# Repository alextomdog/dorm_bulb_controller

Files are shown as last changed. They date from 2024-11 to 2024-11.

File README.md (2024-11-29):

# 项目概述
这是一个用于在寝室中不用下床开关灯的， 将esp8266作为服务器，通过手机web端进行控制舵机运动从而拨动开关的一个项目。

# 演示链接和焊接视频
焊接视频：https://www.bilibili.com/video/BV1LpzrY1Ee3/?vd_source=3774f0978f9f143e4c2fcfed1f5bf447
演示视频：https://www.bilibili.com/video/BV1DSzBYhEJo/

# 功能
1.使用电池，可以实现断电后继续运行

2.支持充电功能

3.使用wifi传输数据

# 物料清单
## 材料
-----------------
| 物料名称 | 数量  |
| :---: | :---: |
| esp8266开发板 | 1 |
| 导线 | 若干  |
| sg90舵机 | 1 |
| SS12F48开关 | 1 |
| M2x10十字头螺栓 | 8 |
| M2螺母 | 4 |
| M3x5十字头螺栓 | 2 |
| tp4056锂电池充电模块 | 1 |
| 18650锂电池 | 1 |
| 18650正负极电池片(一对) | 2 |
| s9013三极管(npn) | 1 |
| 3d打印外壳配件-框架底座(./stl目录) | 1 |
| 3d打印外壳配件-电池盖子(./stl目录) | 1 |
> Note

可以访问：https://makerworld.com/zh/models/832762#profileId-777419 
使用A1Mini 通过bambuStudio打开从而进行打印

## 工具
-----------------
| 工具名称 | 数量  |
| :---: | :---: |
| 锡膏 | 1 |
| 烙铁丝 | 1 |
| 电烙铁 | 1 |
| 剥线钳(可选) | 1 |
| 十字头螺丝刀 | 1 |

# 代码下载使用
1.确保电脑安装了`arduino IDE`

2.确保在`arduino IDE`中配置了`esp8266`的环境

3.下载相关库文件
```c
ESPAsyncTCP
ESPAsyncWebServer
ArduinoJson
Servo
```

4.将代码文件`./program/program.ino`上传到esp8266中

# 电路连接图
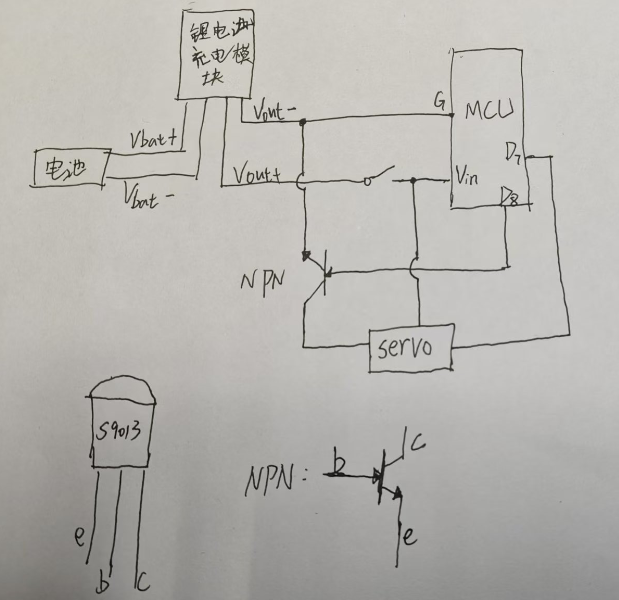
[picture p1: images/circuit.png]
circuit


# web端的使用说明

1. 手机连接到esp8266的wifi，默认wifi名称`dormitory`, 密码为`123456789`(可以在后期web页面的`settings`选项卡中进行修改)
   
2. 打开浏览器，输入静态ip地址:`192.168.192.1`，即可进入web页面进行控制
   
3. web端展示如下图，代码细节参考`/web_page/index.html`文件
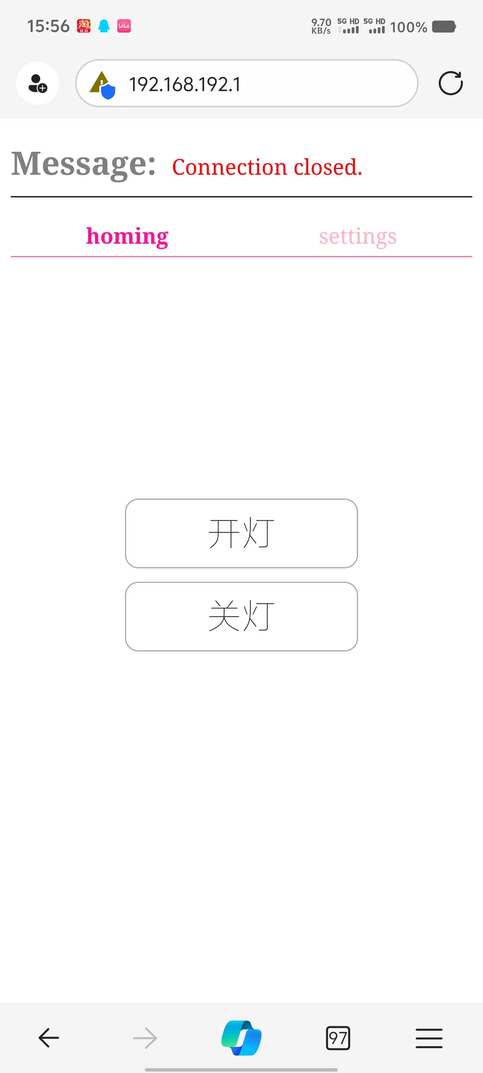
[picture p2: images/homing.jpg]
homing

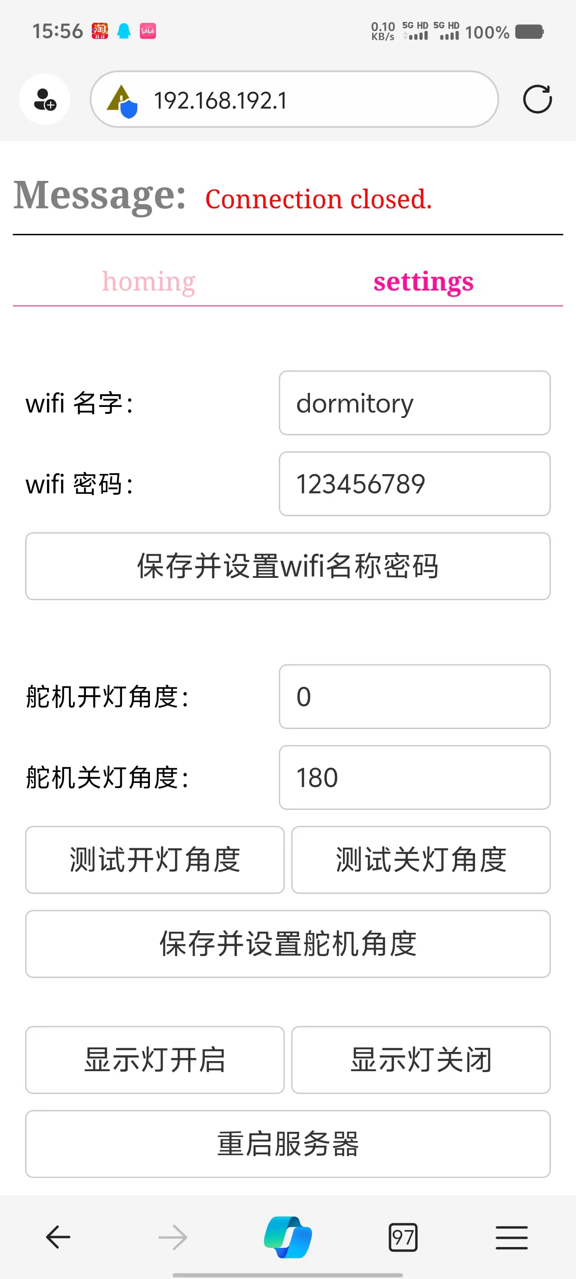
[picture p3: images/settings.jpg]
settings


# 其他说明

1.`/compress`文件夹放置的是用来压缩`html`文件的python代码，使用方法如下：
> `python compress.py path/to/your/html_file`

2.在进行开关灯之前

3.如果遇到连接到esp_wifi之后无法打开静态`ip`地址的情况，请断开数据流量之后再次从浏览器中打开`192.168.192.1`这个`ip`地址。存在部分手机如果检测到当前的wifi无法连接到互联网从而选择会走流量，导致无法访问`ip`地址。

4.连接到esp_wifi之后，是**无法访问互联网**的，需要断开连接之后才可以继续上网

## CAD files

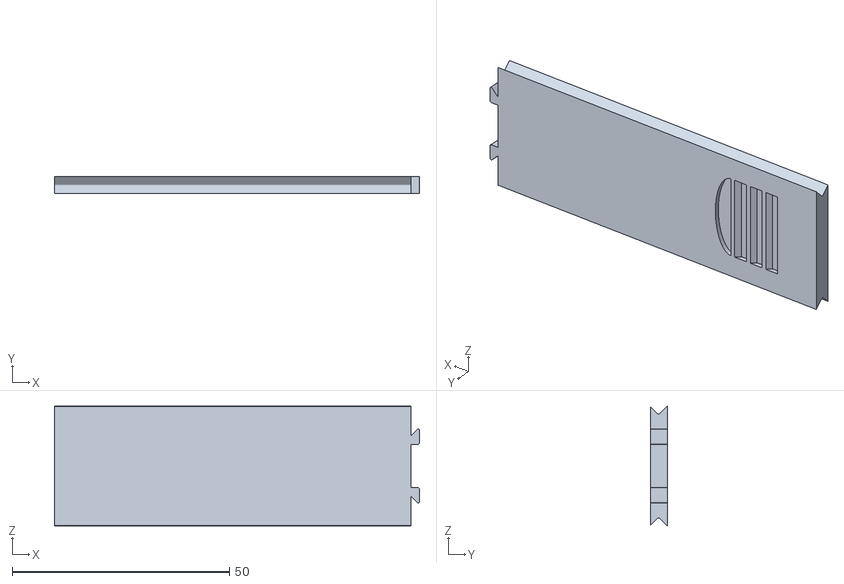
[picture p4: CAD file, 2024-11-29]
stl/电池盖子.STL
84.0 x 3.85 x 27.6

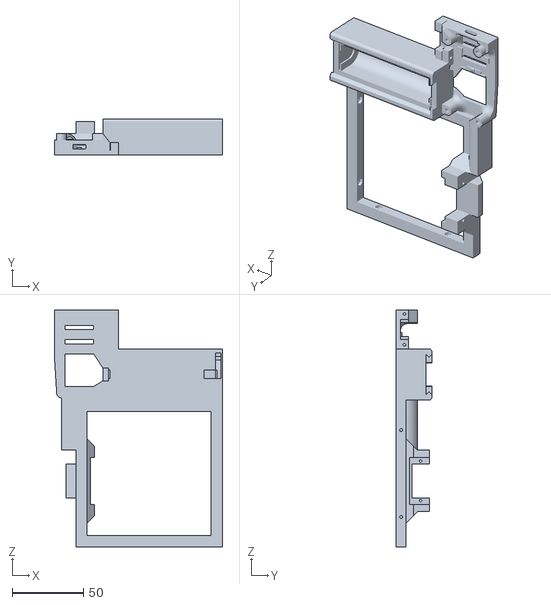
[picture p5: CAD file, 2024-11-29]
stl/框架底座.STL
118.0 x 25.0 x 166.2

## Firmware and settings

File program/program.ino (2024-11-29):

#include <ESP8266WiFi.h>
#include <ESPAsyncTCP.h>
#include <ESPAsyncWebServer.h>
#include <ArduinoJson.h>
#include <FS.h> // 引入文件系统库
#include <Ticker.h>
#include <Servo.h> // 引入舵机库
#define CONFIG_FILENAME "/config.json"
#define CONFIG_SERVO_FILENAME "/servo.json"
#define CONFIG_POWER_LED_FILENAME "/power_led.json"

Ticker timeoutTickerForEspRestart;

JsonDocument config_json;
JsonDocument config_servo_json;
JsonDocument config_power_led_json;

String ssid = "dormitory";
String password = "123456789";

AsyncWebServer server(80); // Create AsyncWebServer object on port 80
AsyncWebSocket ws("/ws");  // Create a WebSocket object

// 设置静态IP
IPAddress local_ip(192, 168, 192, 1); // 设置静态IP地址
IPAddress gateway(192, 168, 1, 1);	  // 设置网关
IPAddress subnet(255, 255, 255, 0);	  // 设置子网掩码

// ===================== HTML ===========================
const char HTML[] PROGMEM = R"rawliteral(
<!DOCTYPE html><html lang="en"><head><meta charset="UTF-8"><meta name="viewport" content="width=device-width, initial-scale=1.0"><title>WebSocket Demo</title><style>.container {display: flex;flex-direction: column;align-items: center;font: 20px Arial, sans-serif;}.setting_line {display: flex;flex-direction: row;align-items: center;justify-content: space-between;width: 100%;margin: 10px 0;}.setting_line label {width: 50%;font-size: 16px;font-weight: normal;display: inline-block;text-align: left;margin-right: 10px;line-height: 2;}.setting_line input {width: 50%;padding: 10px;border-radius: 5px;border: 1px solid #ccc;font-size: 16px;color: #333;background-color: #fff;transition: all 0.3s ease;}.setting_line input:hover {border-color: #888;background-color: #f9f9f9;}.setting_line input:focus {outline: none;border-color: #5b9bd5;box-shadow: 0 0 5px rgba(91, 155, 213, 0.5);}.setting_line button {font-size: large;width: 100%;padding: 10px 20px;border-radius: 5px;border: 1px solid #ccc;background-color: #fff;color: #333;cursor: pointer;transition: all 0.3s ease;}#info {color: red;font-weight: 400;font-size: medium;margin-left: 5px;}h2 {border-bottom: 1px solid #000;padding-bottom: 10px;}.nav {display: flex;flex-direction: row;justify-content: space-around;width: 100%;border-bottom: 1px solid hotpink;color: lightpink;padding-bottom: 5px;margin-bottom: 30px;}.nav_active {color: deeppink;font-weight: bold;}.btn-group {display: flex;flex-direction: column;justify-content: space-around;width: 100%;gap: 10px;}.btn-group button {font-size: 26px;width: 100%;font-weight: lighter;padding: 10px 60px;border-radius: 10px;border: 1px solid darkgray;background-color: #fff;color: #333;cursor: pointer;transition: all 0.3s ease;}.btn-group button:hover {background-color: #f0f0f0;border-color: #999;color: #000;}.btn-group button:focus {outline: none;box-shadow: 0 0 8px rgba(0, 0, 0, 0.2);}.btn-group button:active {background-color: #e0e0e0;border-color: #666;color: #222;transform: scale(0.98);}.setting_line button:hover {background-color: #f0f0f0;border-color: #999;color: #000;}.setting_line button:focus {outline: none;box-shadow: 0 0 8px rgba(0, 0, 0, 0.2);}.setting_line button:active {background-color: #e0e0e0;border-color: #666;color: #222;transform: scale(0.98);}.</style></head><body><h2 style="color: gray;">Message: <span id="info">message bar</span></h2><div class="nav"><div class="nav_active" onclick="page1()" id="page1Nav">homing</div><div onclick="page2()" id="page2Nav">settings</div></div><div class="container"><div class="page1" style="display: block;"><!-- <button onclick="sayHello()">say hello</button> --><div class="btn-group" style="margin-top: 150px;"><button onclick="light_on_bulb()">开灯</button><button onclick="light_off_bulb()">关灯</button></div></div><div class="page2" style="display: none;"><div class="setting_line"><label for="ssid">wifi 名字：</label><input type="text" id="ssid"></div><div class="setting_line"><label for="password">wifi 密码：</label><input type="text" id="password"></div><div class="setting_line"><button onclick="save_wifi_config()">保存并设置wifi名称密码</button></div><div style="height: 20px;"></div><div class="setting_line"><label for="servo_on">舵机开灯角度：</label><input type="text" id="servo_on"></div><div class="setting_line"><label for="servo_off">舵机关灯角度：</label><input type="text" id="servo_off"></div><div class="setting_line"><button onclick="test_servo_on()">测试开灯角度</button><div style="width: 10px;"></div><button onclick="test_servo_off()">测试关灯角度</button></div><div class="setting_line"><button onclick="save_servo_config()">保存并设置舵机角度</button></div><div style="height: 10px;"></div><div class="setting_line"><button onclick="power_led_on()">显示灯开启</button><div style="width: 10px;"></div><button onclick="power_led_off()">显示灯关闭</button></div><div class="setting_line"><button onclick="restart_esp()">重启服务器</button></div></div></div><script>var ws = null;var info = msg => document.getElementById("info").innerHTML = msg;function connect_ws() {try {ws = new WebSocket(`ws://${window.location.hostname}/ws`);ws.onopen = function (evt) {info("Connection open...");};ws.onmessage = on_message;ws.onclose = function (evt) {info("Connection closed.");ws = null;};ws.onerror = function (evt) {info("Connection error.");ws = null;};} catch (e) {ws = null;info("Connection error.");}};function send_message(json_data) {if (ws === null || ws.readyState !== WebSocket.OPEN) {connect_ws();} else {ws.send(JSON.stringify(json_data));}};function on_message(evt) {let data = JSON.parse(evt.data);info(data.message);if (data.cmd === "init") {document.getElementById("ssid").value = data.wifi_config.ssid;document.getElementById("password").value = data.wifi_config.password;document.getElementById("servo_on").value = data.servo_config.servo_on;document.getElementById("servo_off").value = data.servo_config.servo_off;};};function validate_angle(string_value) {let value = parseInt(string_value);if (value < 0) {info("角度不能小于0");return false;} else if (value > 180) {info("角度不能大于180");return false;} else {return value;};};function test_servo_on() {let value = validate_angle(document.getElementById("servo_on").value);if (value !== false) {send_message({ "cmd": "set_angle", "angle": value + "" });};};function test_servo_off() {let value = validate_angle(document.getElementById("servo_off").value);if (value !== false) {send_message({ "cmd": "set_angle", "angle": value + "" });};};function save_servo_config() {let servo_on = validate_angle(document.getElementById("servo_on").value);let servo_off = validate_angle(document.getElementById("servo_off").value);if (servo_on !== false && servo_off !== false) {send_message({ "cmd": "save_servo_config", "servo_on": servo_on + "", "servo_off": servo_off + "" });};};function validate_wifi_config(ssid, password) {if (ssid === "") {info("SSID不能为空");return false;} else if (password === "") {info("密码不能为空");return false;} else {return true;};};function save_wifi_config() {let ssid = document.getElementById("ssid").value;let password = document.getElementById("password").value;if (validate_wifi_config(ssid, password)) {ssid = ssid.trim();password = password.trim();send_message({ "cmd": "save_wifi_config", "ssid": ssid, "password": password });};};function restart_esp() {send_message({ "cmd": "restart_esp" });};function power_led_on() {send_message({ "cmd": "power_led_on" });};function power_led_off() {send_message({ "cmd": "power_led_off" });};function light_on_bulb() {send_message({ "cmd": "light_on_bulb" });};function light_off_bulb() {send_message({ "cmd": "light_off_bulb" });};function page1() {document.querySelector(".page1").style.display = "block";document.getElementById("page1Nav").classList.add("nav_active");document.getElementById("page2Nav").classList.remove("nav_active");document.querySelector(".page2").style.display = "none";}function page2() {document.querySelector(".page1").style.display = "none";document.getElementById("page1Nav").classList.remove("nav_active");document.getElementById("page2Nav").classList.add("nav_active");document.querySelector(".page2").style.display = "block";}window.onload = function () {connect_ws();};</script></body></html>
)rawliteral";

// 时间相关的操作
unsigned long timeout_duration = 2000; // 5秒
unsigned long current_call_servo_moving_time = 0;

// ===================== 舵机操作 =========================
Servo servo;
#define ServoPin D7
#define transistor_pin D8

void servo_setup()
{
	servo.attach(ServoPin);

	// 初始化三极管base控制端
	pinMode(transistor_pin, OUTPUT);

	int servo_on = config_servo_json["servo_on"];
	int servo_off = config_servo_json["servo_off"];
	int servo_middle = (servo_on + servo_off) / 2;
	servo_move(servo_middle); // reset servo position

	delay(600); // delay for servo moving complete
}

void servo_move(int angle)
{
	// 每次调用都保存当前的时间
	current_call_servo_moving_time = millis(); // 获取当前时间
	// 将D8口设置为高电平，使三极管导通
	digitalWrite(transistor_pin, HIGH);
	servo.write(angle);
}

void light_on_bulb()
{
	int servo_on = config_servo_json["servo_on"];
	int servo_off = config_servo_json["servo_off"];
	int servo_middle = (servo_on + servo_off) / 2;
	servo_move(servo_on);
	// delay for servo moving complete
	delay(700);
	servo_move(servo_middle); // reset servo position
}

void light_off_bulb()
{
	int servo_on = config_servo_json["servo_on"];
	int servo_off = config_servo_json["servo_off"];
	int servo_middle = (servo_on + servo_off) / 2;
	servo_move(servo_off);
	// delay for servo moving complete
	delay(700);
	servo_move(servo_middle); // reset servo position
}

// =====================电源指示灯========================
void power_led_setup()
{
	pinMode(2, OUTPUT);
	String power_led_status = config_power_led_json["status"];
	if (power_led_status == "1")
	{
		power_led_on();
	}
	else if (power_led_status == "0")
	{
		power_led_off();
	}
}

void power_led_on()
{
	digitalWrite(2, LOW);
}

void power_led_off()
{
	digitalWrite(2, HIGH);
}

// ===================== 文件操作 ===========================

void write_json_file(String filename, JsonDocument json_document)
{
	File file = SPIFFS.open(filename, "w");
	serializeJson(json_document, file);
	file.close();
}

JsonDocument read_json_file(String filename)
{
	File file = SPIFFS.open(filename, "r");
	JsonDocument json_document;
	deserializeJson(json_document, file);
	file.close();
	return json_document;
}

// 配置文件初始化函数，接收回调函数作为参数
void init_json_file(const char *json_filename, void (*config_func)(JsonDocument &))
{
	// 判断文件是否存在
	if (!SPIFFS.exists(json_filename))
	{
		Serial.print("create config file: ");
		Serial.println(json_filename);

		JsonDocument json_document;
		// 调用传入的回调函数来修改 json_document
		config_func(json_document);

		// 写入 JSON 文件
		write_json_file(json_filename, json_document);
	}
	else
	{
		Serial.print("config file: ");
		Serial.print(json_filename);
		Serial.println(" has been exist.");
	}
}

void handle_config_file_init_callback(JsonDocument &json_document)
{
	// 在这里初始化 JSON 文档
	json_document["ssid"] = ssid;
	json_document["password"] = password;
}

void handle_config_servo_init_callback(JsonDocument &json_document)
{
	json_document["servo_on"] = "0";
	json_document["servo_off"] = "180";
}

void handle_config_power_led_init_callback(JsonDocument &json_document)
{
	// 这里只使用0和1，所以不需要处理字符串
	json_document["status"] = "1";
}

void spiff_file_system_setup()
{
	if (!SPIFFS.begin())
	{
		Serial.println("An Error has occurred while mounting SPIFFS");
		Serial.println("try to format SPIFFS partition");
		if (SPIFFS.format())
		{
			Serial.println("SPIFFS partition formatted successfully");
			ESP.restart();
		}
		else
		{
			Serial.println("SPIFFS partition format failed");
		}
		return;
	}
	else
	{
		Serial.println("SPIFFS initalized successfully");
		init_json_file(CONFIG_FILENAME, handle_config_file_init_callback);
		init_json_file(CONFIG_SERVO_FILENAME, handle_config_servo_init_callback);
		init_json_file(CONFIG_POWER_LED_FILENAME, handle_config_power_led_init_callback);
	}
}

// ===================================== 处理 WebSocket 消息 =====================================

void on_request_response_ws_message(JsonDocument &request_json_data, JsonDocument &response_json_data)
{
	String cmd = request_json_data["cmd"];
	if (cmd == "set_angle")
	{
		int angle = request_json_data["angle"];
		if (angle >= 0 && angle <= 180)
		{
			servo_move(angle);
			response_json_data["message"] = "成功设置角度: " + String(angle) + "°";
		}
		else
		{
			response_json_data["message"] = "角度设置失败: " + String(angle) + "°";
		}
	}
	else if (cmd == "save_servo_config")
	{
		response_json_data["message"] = "成功保存舵机配置";
		config_servo_json["servo_on"] = request_json_data["servo_on"];
		config_servo_json["servo_off"] = request_json_data["servo_off"];
		// 保存到文件
		write_json_file(CONFIG_SERVO_FILENAME, config_servo_json);
	}
	else if (cmd == "save_wifi_config")
	{
		response_json_data["message"] = "成功保存wifi配置,重启生效";
		config_json["ssid"] = request_json_data["ssid"];
		config_json["password"] = request_json_data["password"];
		// 保存到文件
		write_json_file(CONFIG_FILENAME, config_json);
	}
	else if (cmd == "restart_esp")
	{
		response_json_data["message"] = "1s后重启服务器";
		timeoutTickerForEspRestart.attach(1, ESP.restart);
	}
	else if (cmd == "power_led_on")
	{
		response_json_data["message"] = "打开电源指示灯";
		config_power_led_json["status"] = "1";
		// 保存到文件
		write_json_file(CONFIG_POWER_LED_FILENAME, config_power_led_json);
		power_led_on();
	}
	else if (cmd == "power_led_off")
	{
		response_json_data["message"] = "关闭电源指示灯";
		config_power_led_json["status"] = "0";
		// 保存到文件
		write_json_file(CONFIG_POWER_LED_FILENAME, config_power_led_json);
		power_led_off();
	}
	else if (cmd == "light_on_bulb")
	{
		response_json_data["message"] = "打开灯泡";
		light_on_bulb();
	}
	else if (cmd == "light_off_bulb")
	{
		response_json_data["message"] = "关闭灯泡";
		light_off_bulb();
	}
}

void handle_websocket_message_callback(void *arg, uint8_t *data, size_t len)
{
	AwsFrameInfo *info = (AwsFrameInfo *)arg;
	if (info->final && info->index == 0 && info->len == len && info->opcode == WS_TEXT)
	{
		JsonDocument request_json_data;
		JsonDocument response_json_data;
		String serialized_json_document;

		data[len] = 0;
		String message = (char *)data;

		DeserializationError error = deserializeJson(request_json_data, message);

		if (error)
		{
			Serial.print("deserializeJson() failed: ");
			Serial.println(error.c_str());
			return;
		}
		else
		{
			on_request_response_ws_message(request_json_data, response_json_data);
			serializeJson(response_json_data, serialized_json_document);
			ws.textAll(serialized_json_document);
		}
	}
}

void handle_websocket_connected_callback(AsyncWebSocketClient *client)
{
	Serial.println("an user connect the websocket");
	// 向当前连接的用户发送消息
	JsonDocument response_json_data_for_connection;

	response_json_data_for_connection["wifi_config"] = config_json;
	response_json_data_for_connection["servo_config"] = config_servo_json;
	response_json_data_for_connection["message"] = "连接ESP成功";
	response_json_data_for_connection["cmd"] = "init";

	String serialized_json_document;
	serializeJson(response_json_data_for_connection, serialized_json_document);
	client->text(serialized_json_document);
}

void on_event(AsyncWebSocket *server, AsyncWebSocketClient *client, AwsEventType type, void *arg, uint8_t *data, size_t len)
{
	switch (type)
	{
	case WS_EVT_CONNECT:
		Serial.printf("WebSocket client #%u connected from %s\n", client->id(), client->remoteIP().toString().c_str());
		handle_websocket_connected_callback(client);
		break;
	case WS_EVT_DISCONNECT:
		Serial.printf("WebSocket client #%u disconnected\n", client->id());
		break;
	case WS_EVT_DATA:
		handle_websocket_message_callback(arg, data, len);
		break;
	case WS_EVT_PONG:
	case WS_EVT_ERROR:
		break;
	}
}

void setup_wifi()
{
	Serial.print("Setting AP (Access Point)…");
	const char *ssid_ = config_json["ssid"];
	const char *password_ = config_json["password"];
	WiFi.softAP(ssid_, password_);

	// 设置静态IP
	if (!WiFi.softAPConfig(local_ip, gateway, subnet))
	{
		Serial.println("Failed to configure AP");
	}
	else
	{
		Serial.println("AP Static IP Configured");
	}

	// 输出AP的IP地址
	Serial.print("AP IP Address: ");
	Serial.println(WiFi.softAPIP());

	server.on("/", HTTP_GET, [](AsyncWebServerRequest *request)
			  { request->send_P(200, "text/html", HTML); });
	ws.onEvent(on_event);
	server.addHandler(&ws);
	server.begin();
}

void setup()
{
	Serial.begin(115200);

	spiff_file_system_setup();

	config_json = read_json_file(CONFIG_FILENAME);
	config_servo_json = read_json_file(CONFIG_SERVO_FILENAME);
	config_power_led_json = read_json_file(CONFIG_POWER_LED_FILENAME);

	power_led_setup();
	servo_setup();

	Serial.print("config_json: ");
	Serial.print("ssid: ");
	Serial.print((String)config_json["ssid"]);
	Serial.print("; password:");
	Serial.print((String)config_json["password"]);
	Serial.println();

	setup_wifi();
}

void loop()
{
	// 判断时间是否超出界限
	if (millis() - current_call_servo_moving_time > timeout_duration)
	{
		// 关闭三极管
		digitalWrite(transistor_pin, LOW);
	}
}
